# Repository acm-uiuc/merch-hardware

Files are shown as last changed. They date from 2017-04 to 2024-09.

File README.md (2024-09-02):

# Hardware to make Merch function



All the designs for the hardware components of Merch are found here.

## Components

### Vending Machine

This machine is a Dixie Narco 5800 Bevmax **4**, **not a Bevmax 3 machine**.

### Merch Hat

This unofficial Raspberry-Pi Hat allows a Pi to emulate keypresses on the machine's keypad.

### iPad Mount

### Connection Pictures

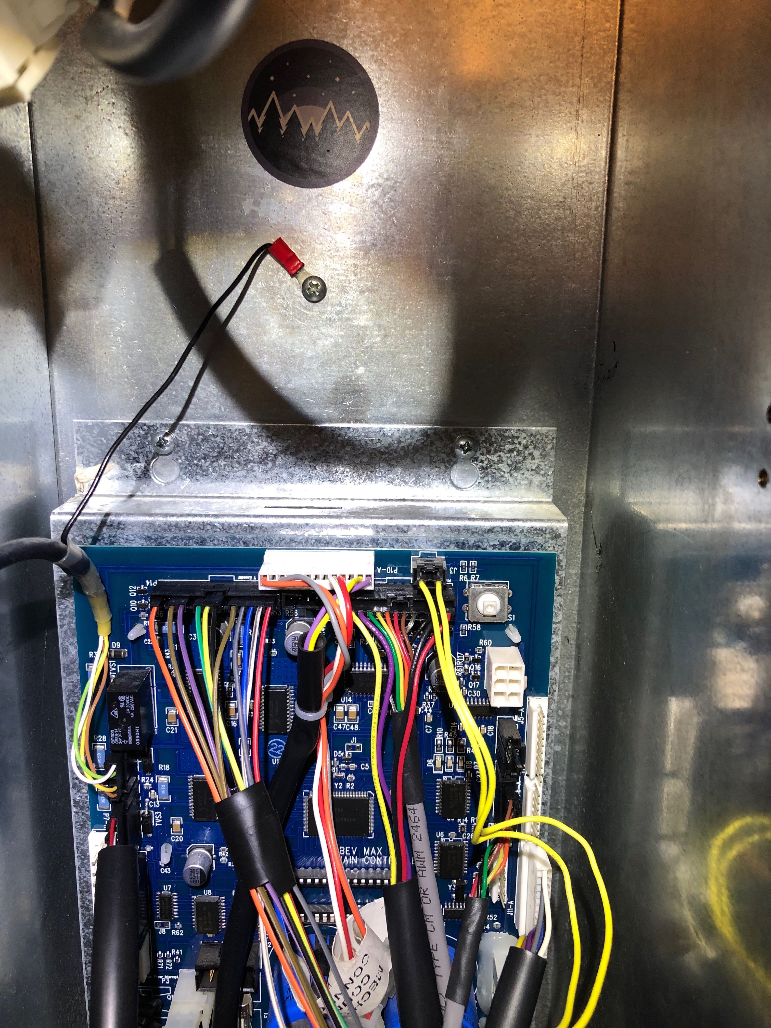
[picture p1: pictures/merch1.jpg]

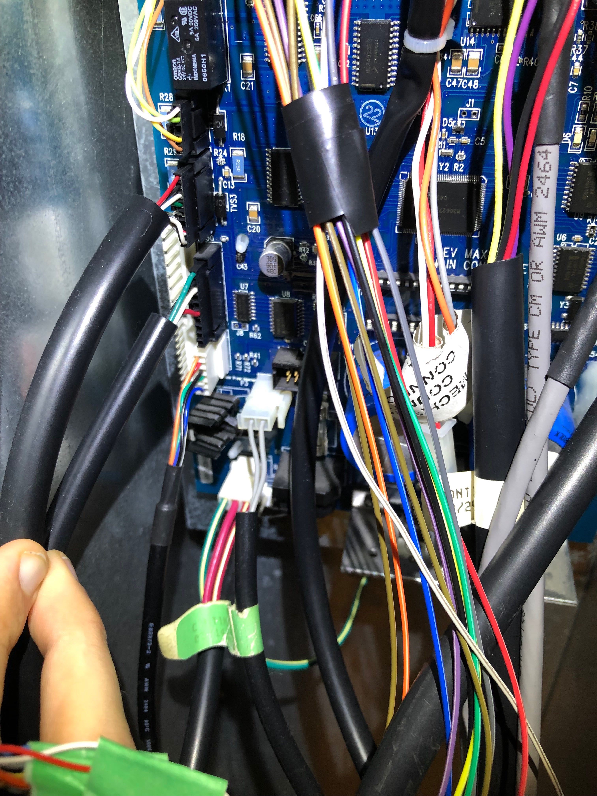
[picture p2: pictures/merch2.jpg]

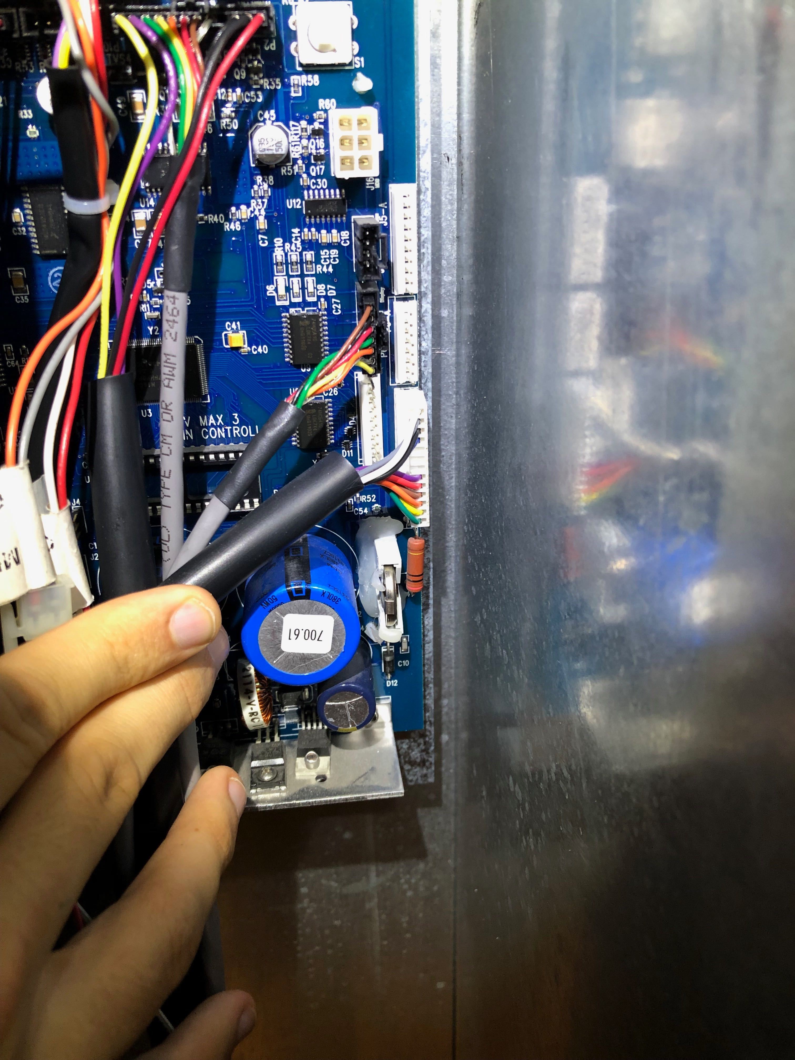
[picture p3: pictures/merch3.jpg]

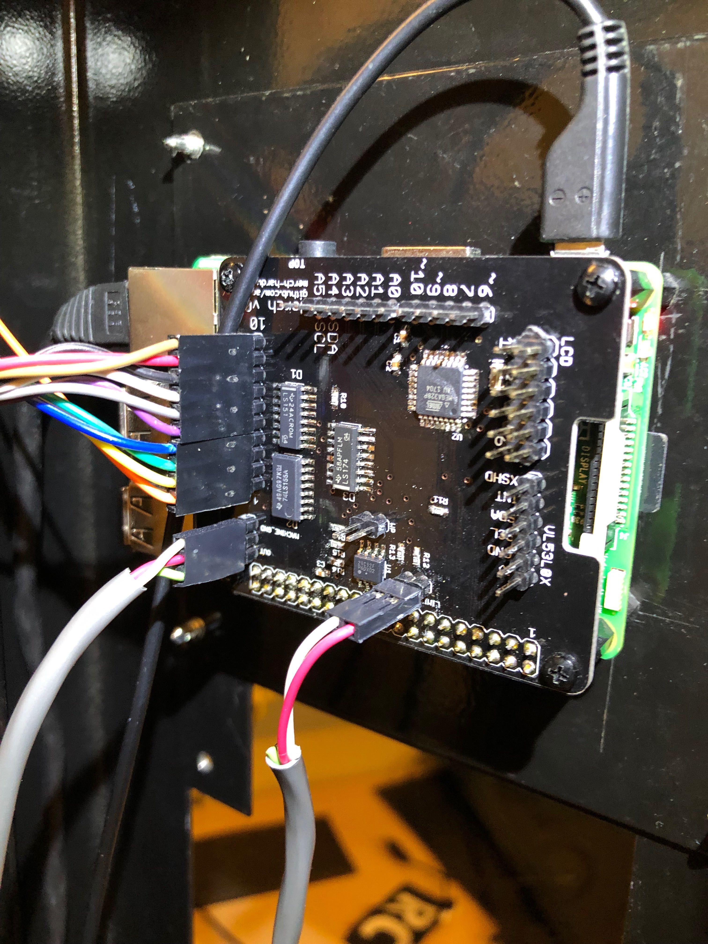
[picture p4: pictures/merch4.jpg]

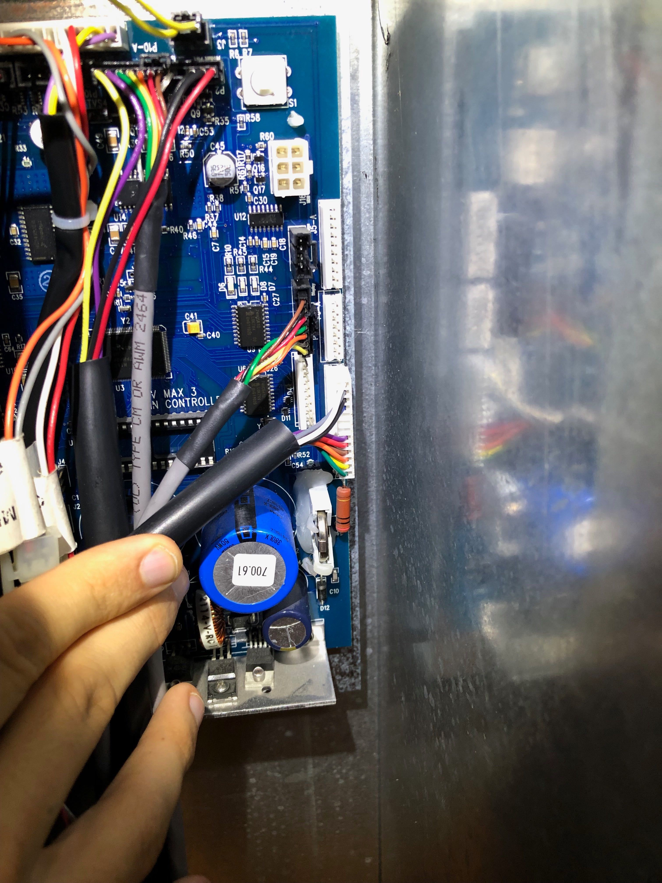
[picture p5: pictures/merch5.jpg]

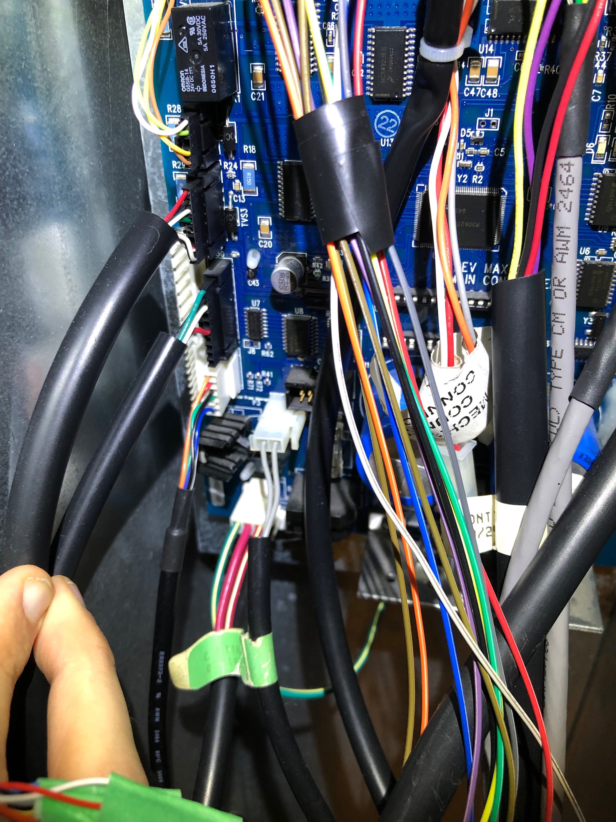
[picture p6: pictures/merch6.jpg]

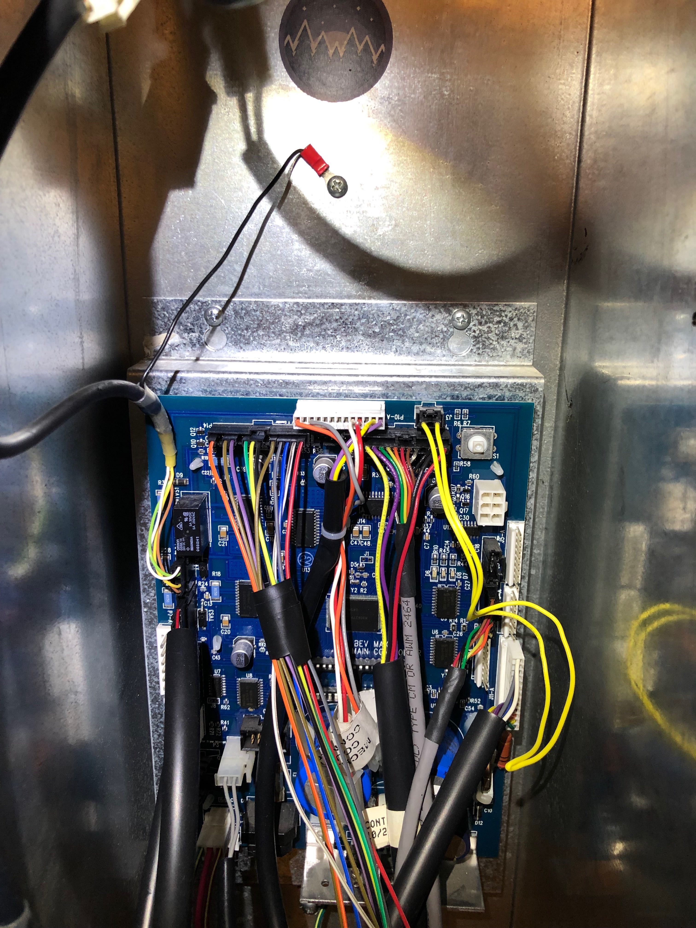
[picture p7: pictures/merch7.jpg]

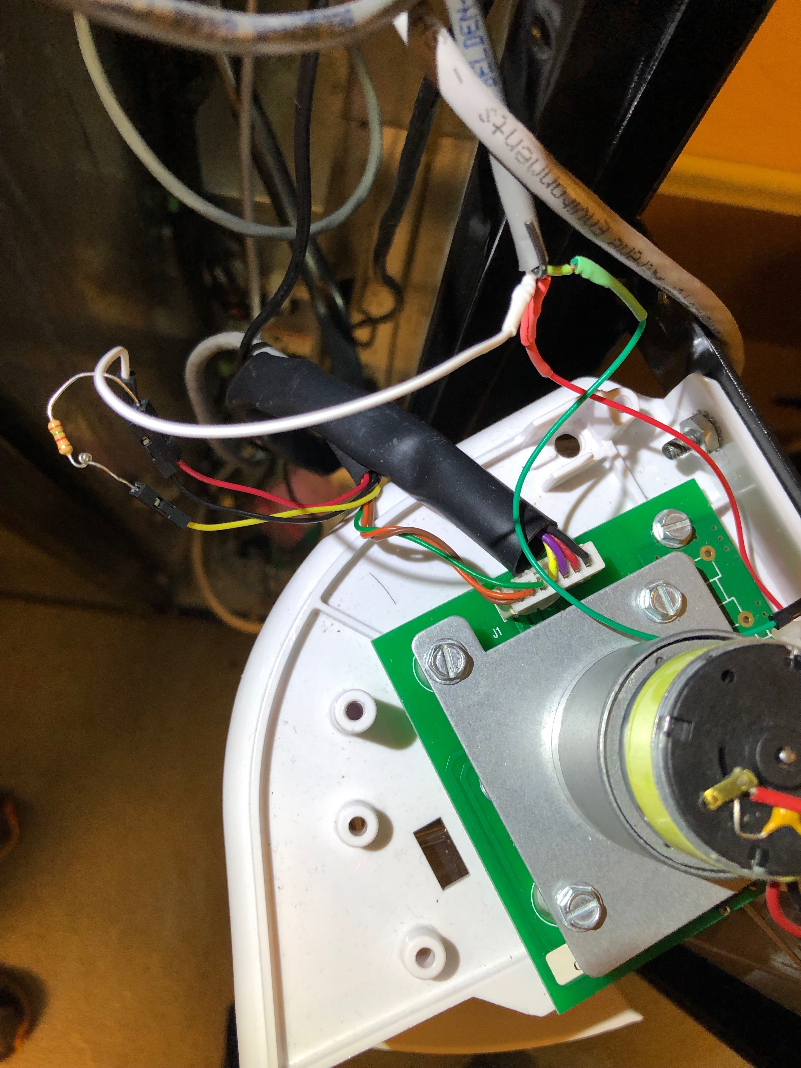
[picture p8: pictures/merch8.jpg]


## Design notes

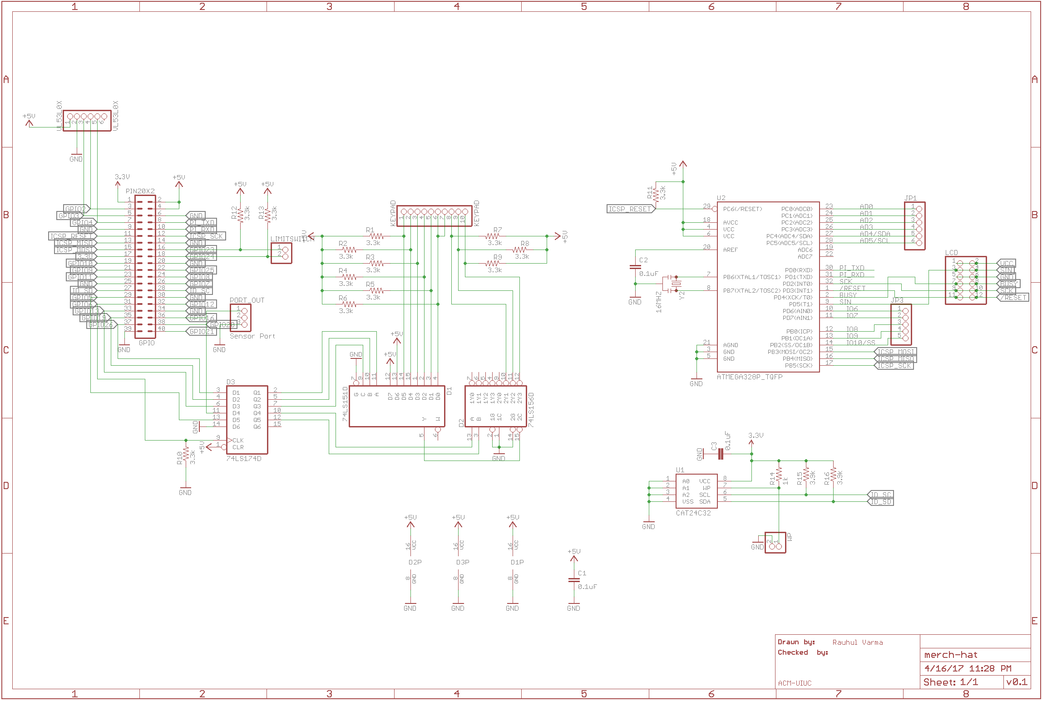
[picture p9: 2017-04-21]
keypad_pcb_surface_mount/Schematic.png

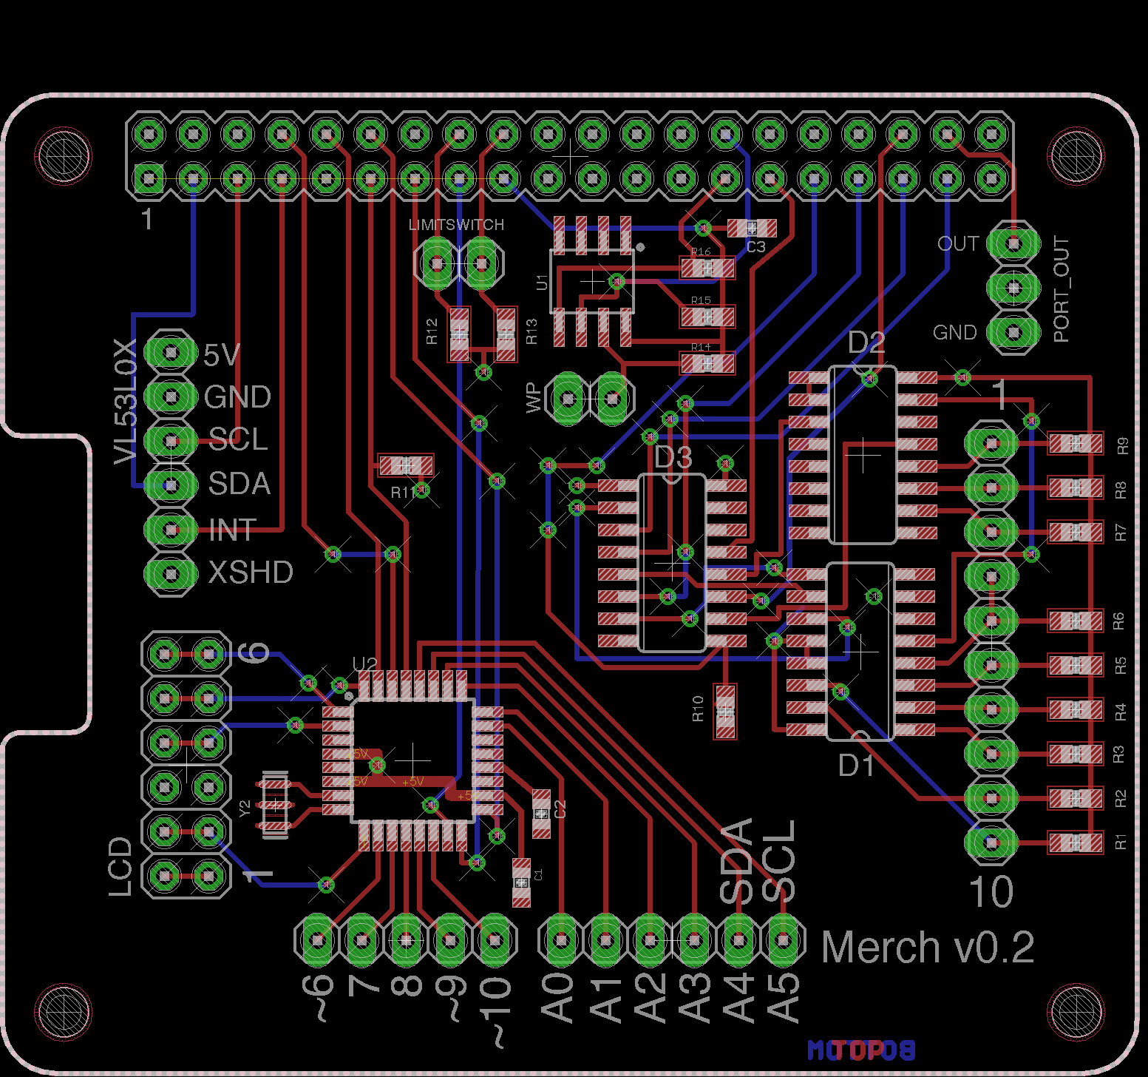
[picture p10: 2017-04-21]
keypad_pcb_surface_mount/BoardLayout.png

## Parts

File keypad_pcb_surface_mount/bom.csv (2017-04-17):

Location | MPN/Seeed SKU | Quantity
C1,C2,C3 | 302010138 | 3
R1,R2,R3,R4,R5,R6,R7,R8,R9,R10,R11,R12,R13 | 301010251 | 13
D1 | SN74LS151D | 1
D2 | SN74LS155D | 1
D3 | SN74LS174D | 1
R14 | 301010291 | 1
R15,R16 | RC0603JR-073K9L | 2
U1 | CAT24C32WI-G | 1
U2 | ATMEGA328P-AUR | 1
Y2 | CSTCE16MOV53-R0 | 1

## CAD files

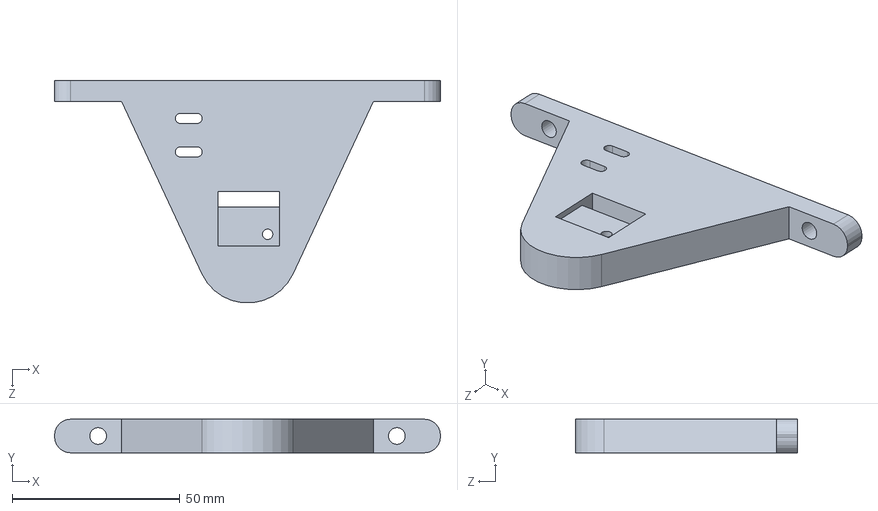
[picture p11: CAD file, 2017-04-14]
port_sensor_mount/sensor_mount.SLDPRT
115.0 x 10.0 x 66.3 mm

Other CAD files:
port_sensor_mount/sensor_mount.STL

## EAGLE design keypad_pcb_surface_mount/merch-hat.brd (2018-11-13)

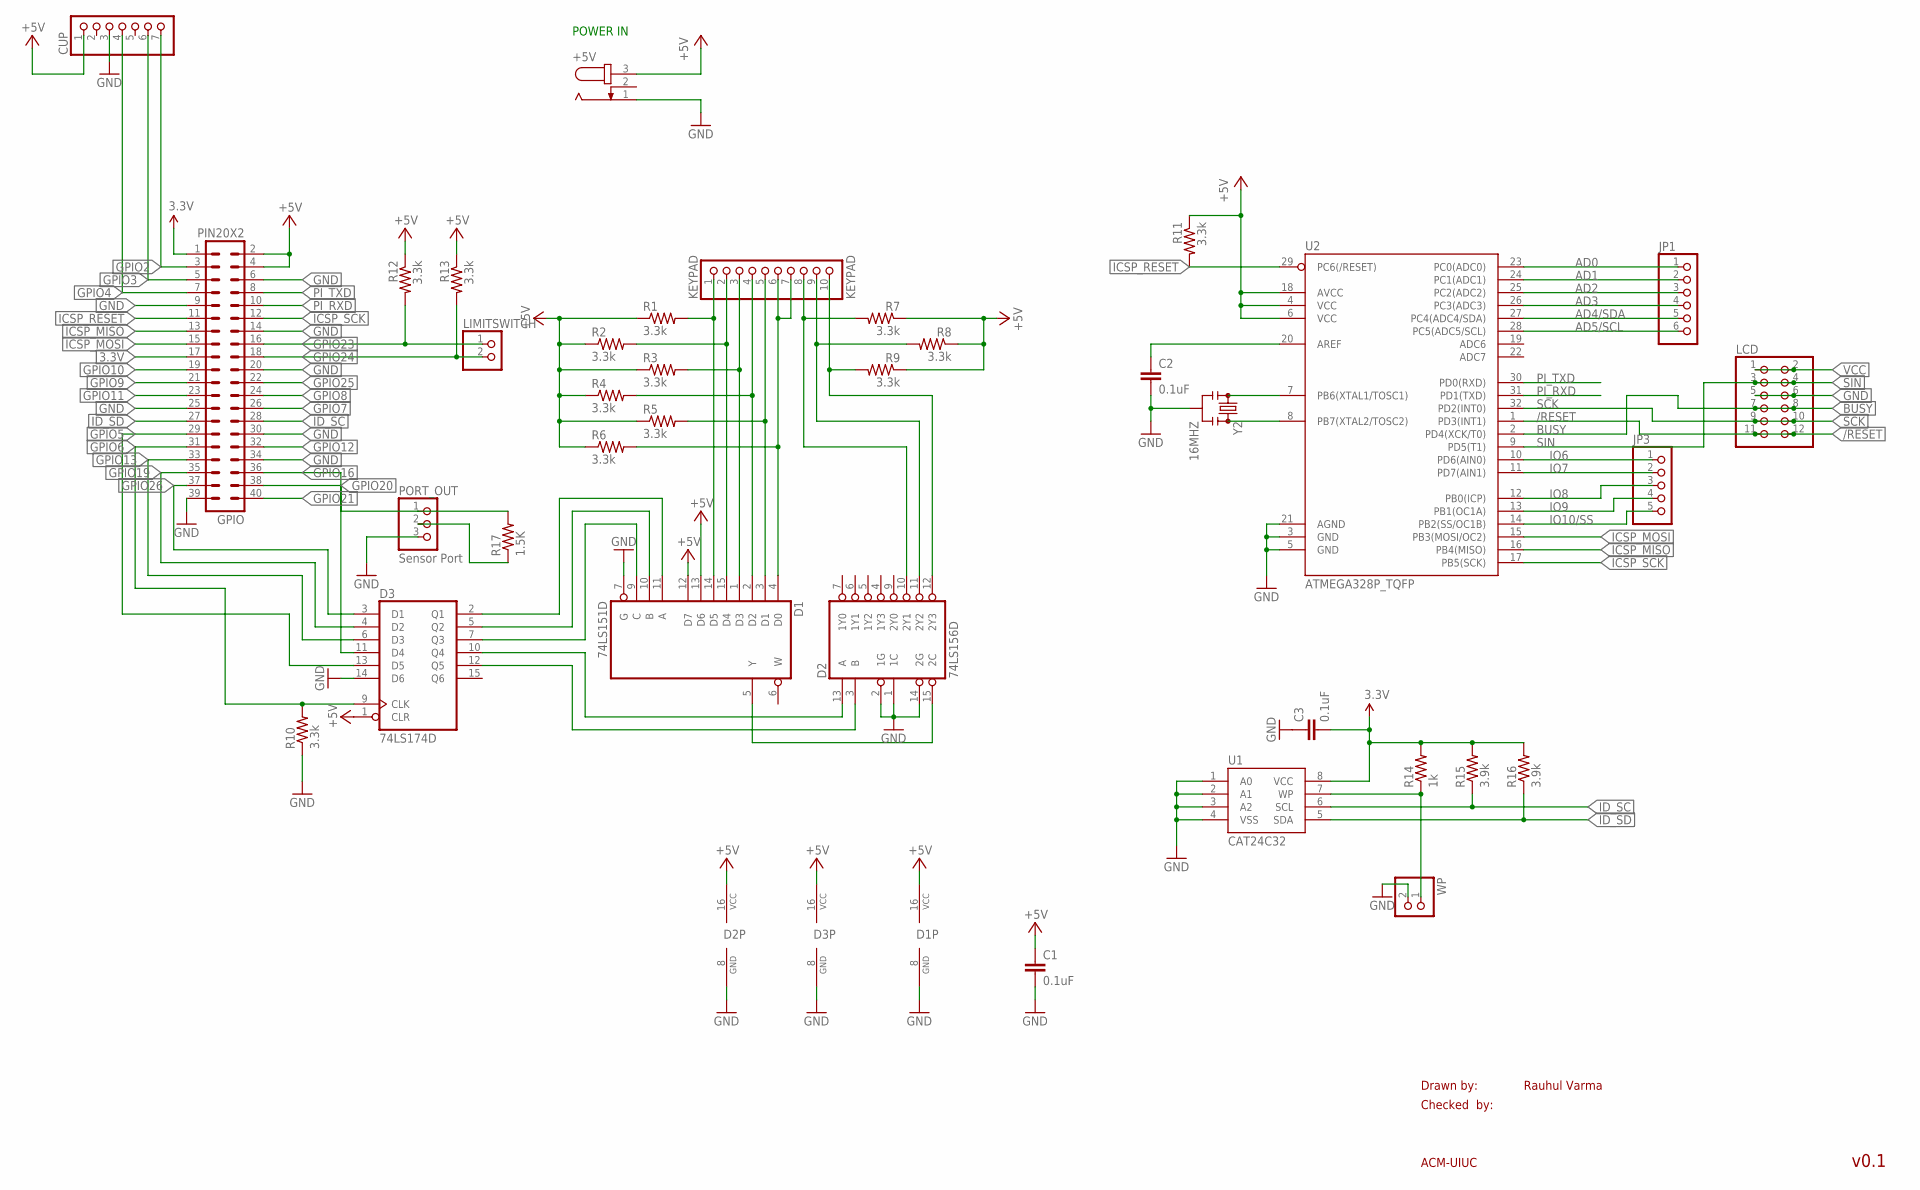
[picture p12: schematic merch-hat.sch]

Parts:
+5V: JACK-PLUG1; SPC4078
C1, C2, C3: 0.1uF; 0603-CAP
CUP: PINHD-1X7; 1X07
D1: 74LS151D; SO16
D2: 74LS156D; SO16
D3: 74LS174D; SO16
GPIO: PIN20X2; PIN_20X2
JP1: PINHD-1X6; 1X06
JP3: PINHD-1X5; 1X05
KEYPAD: KEYPAD; 1X10
LCD: PINHD-2X6; 2X06
LIMITSWITCH: PINHD-1X2; 1X02
PORT_OUT: Sensor Port; 1X03
R1, R2, R3, R4, R5, R6, R7, R8, R9, R10, R11, R12, R13: 3.3k; 0603-RES
R14: 1k; 0603-RES
R15, R16: 3.9k; 0603-RES
R17: 1.5K; R0603
U1: CAT24C32; SO08
U2: ATMEGA328P_TQFP; TQFP32-08
WP: PINHD-1X2; 1X02
Y2: 16MHZ; RESONATOR-SMD

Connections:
3.3V: C3.2, GPIO.1, GPIO.17, R14.2, R15.2, R16.2, U1.8 (VCC)
+5V: +5V.3, C1.1, CUP.1, D1.12 (D7), D1.13 (D6), D1.16 (VCC), D2.16 (VCC), D3.1 (CLR), D3.16 (VCC), GPIO.2, GPIO.4, R1.1, R2.1, R3.1, R4.1, R5.1, R6.1, R7.1, R8.1, R9.1, R11.1, R12.1, R13.1, U2.4 (VCC), U2.6 (VCC), U2.18 (AVCC)
/RESET: LCD.11, LCD.12, U2.1 (PD3(INT1))
AD0: JP1.1, U2.23 (PC0(ADC0))
AD1: JP1.2, U2.24 (PC1(ADC1))
AD2: JP1.3, U2.25 (PC2(ADC2))
AD3: JP1.4, U2.26 (PC3(ADC3))
AD4/SDA: JP1.5, U2.27 (PC4(ADC4/SDA))
AD5/SCL: JP1.6, U2.28 (PC5(ADC5/SCL))
BUSY: LCD.7, LCD.8, U2.2 (PD4(XCK/T0))
GND: +5V.1, C1.2, C2.2, C3.1, CUP.3, D1.7 (G), D1.8 (GND), D2.1 (1C), D2.2 (1G), D2.8 (GND), D2.14 (2G), D3.8 (GND), D3.14 (D6), GPIO.6, GPIO.9, GPIO.14, GPIO.20, GPIO.25, GPIO.30, GPIO.34, GPIO.39, LCD.5, LCD.6, PORT_OUT.3, R10.1, U1.1 (A0), U1.2 (A1), U1.3 (A2), U1.4 (VSS), U2.3 (GND), U2.5 (GND), U2.21 (AGND), WP.2, Y2.2
GPIO2: CUP.7, GPIO.3
GPIO3: CUP.6, GPIO.5
GPIO4: CUP.4, GPIO.7
GPIO5: D3.13 (D5), GPIO.29
GPIO6: D3.9 (CLK), GPIO.31, R10.2
GPIO7: GPIO.26
GPIO8: GPIO.24
GPIO9: GPIO.21
GPIO10: GPIO.19
GPIO11: GPIO.23
GPIO12: GPIO.32
GPIO13: D3.6 (D3), GPIO.33
GPIO16: D3.11 (D4), GPIO.36
GPIO19: D3.4 (D2), GPIO.35
GPIO20: GPIO.38, PORT_OUT.1, R17.2
GPIO21: GPIO.40
GPIO23: GPIO.16, LIMITSWITCH.1, R12.2
GPIO24: GPIO.18, LIMITSWITCH.2, R13.2
GPIO25: GPIO.22
GPIO26: D3.3 (D1), GPIO.37
ICSP_MISO: GPIO.13, U2.16 (PB4(MISO))
ICSP_MOSI: GPIO.15, U2.15 (PB3(MOSI/OC2))
ICSP_RESET: GPIO.11, R11.2, U2.29 (PC6(/RESET))
ICSP_SCK: GPIO.12, U2.17 (PB5(SCK))
ID_SC: GPIO.28, R15.1, U1.6 (SCL)
ID_SD: GPIO.27, R16.1, U1.5 (SDA)
IO6: JP3.1, U2.10 (PD6(AIN0))
IO7: JP3.2, U2.11 (PD7(AIN1))
IO8: JP3.3, U2.12 (PB0(ICP))
IO9: JP3.4, U2.13 (PB1(OC1A))
IO10/SS: JP3.5, U2.14 (PB2(SS/OC1B))
unnamed: D1.14 (D5), KEYPAD.1, R1.2
unnamed: R14.1, U1.7 (WP), WP.1
unnamed: PORT_OUT.2, R17.1
unnamed: D1.15 (D4), KEYPAD.2, R2.2
unnamed: D1.1 (D3), KEYPAD.3, R3.2
unnamed: D1.2 (D2), KEYPAD.4, R4.2
unnamed: D1.3 (D1), KEYPAD.5, R5.2
unnamed: D1.11 (A), D3.2 (Q1)
unnamed: D1.4 (D0), KEYPAD.6, KEYPAD.7, R6.2
unnamed: D2.10 (2Y1), KEYPAD.8, R7.2
unnamed: D2.11 (2Y2), KEYPAD.9, R8.2
unnamed: D2.12 (2Y3), KEYPAD.10, R9.2
unnamed: D1.10 (B), D3.5 (Q2)
unnamed: D1.9 (C), D3.7 (Q3)
unnamed: D2.13 (A), D3.10 (Q4)
unnamed: D2.3 (B), D3.12 (Q5)
unnamed: D1.5 (Y), D2.15 (2C)
unnamed: U2.7 (PB6(XTAL1/TOSC1)), Y2.1
unnamed: U2.8 (PB7(XTAL2/TOSC2)), Y2.3
unnamed: C2.1, U2.20 (AREF)
PI_RXD: GPIO.10, U2.31 (PD1(TXD))
PI_TXD: GPIO.8, U2.30 (PD0(RXD))
SCK: LCD.9, LCD.10, U2.32 (PD2(INT0))
SIN: LCD.3, LCD.4, U2.9 (PD5(T1))
VCC: LCD.1, LCD.2

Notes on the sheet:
Drawn by:
Checked by:
ACM-UIUC
Rauhul Varma
v0.1
POWER IN

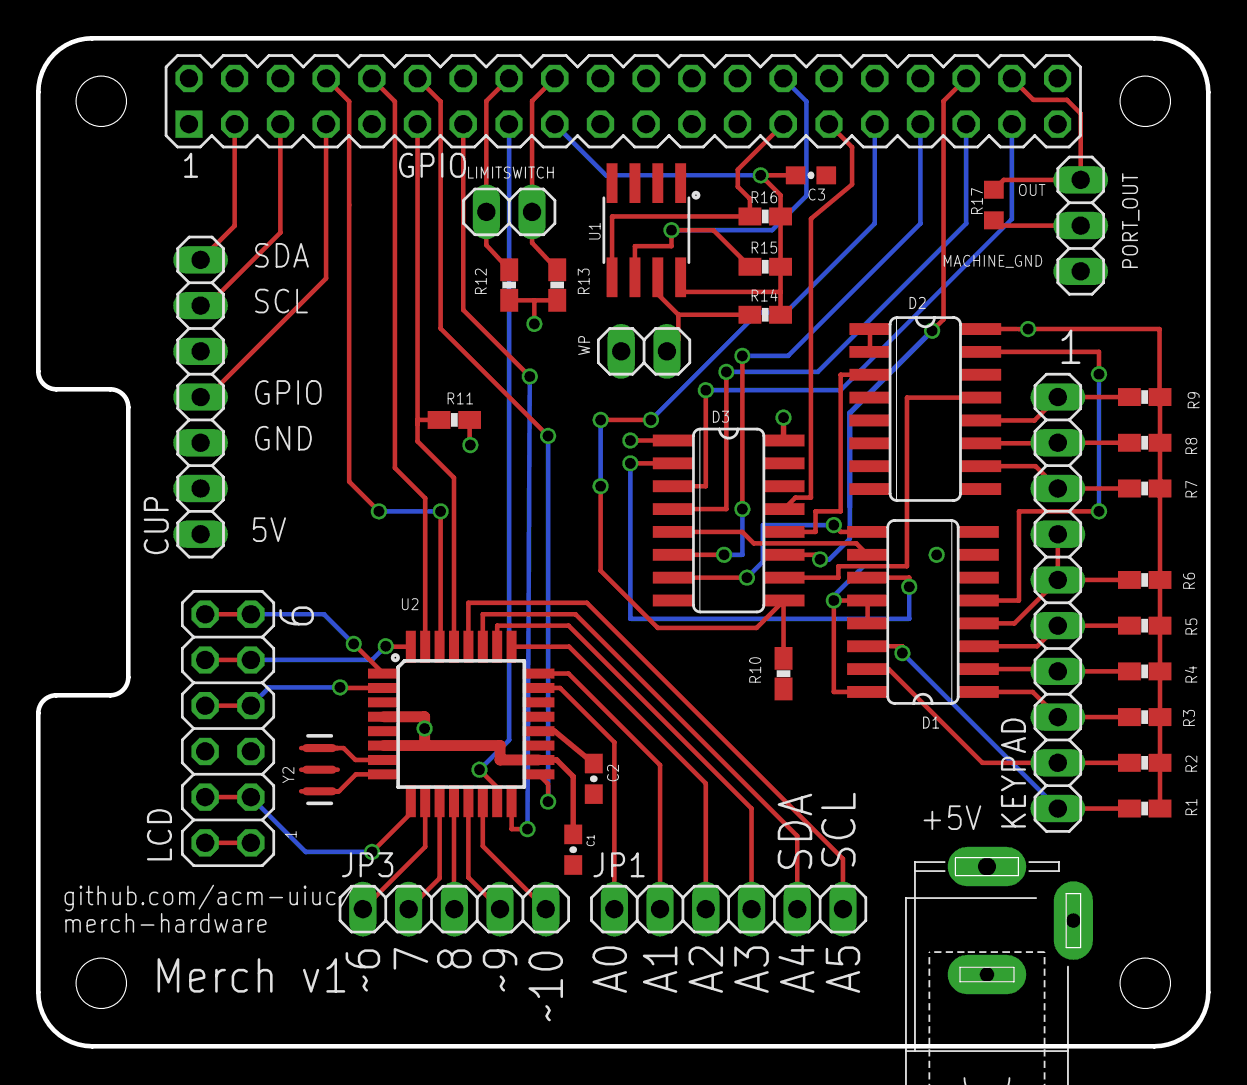
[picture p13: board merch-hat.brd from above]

Board: 2 copper layers, 65.0 x 56.0 mm, 36 parts (0 on the bottom side), 59 nets.

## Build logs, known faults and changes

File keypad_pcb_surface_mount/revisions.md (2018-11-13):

# Pending

# Done
- break out rpi power - maybe add barrel jack
- fix pinout for LoS sensor
- add pullup

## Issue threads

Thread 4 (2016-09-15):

Caffeine Feature Ideas

abrandemuehl, 2016-09-15:
Initial feature ideas:
- NFC and Magnetic stripe reader
  - How to add RFID? The cards use a HID tech
- Coin pay for non members - at higher price
- Touch screen
- Pressure sensors
- Leds everywhere inside
- Automatic Stock Notifications
- Auto purchase stock when empty
- Amazon echo/Voice control
- Data backed purchasing
- Variable pricing

Feel free to post any ideas you have here

Closed 2017-02-24.

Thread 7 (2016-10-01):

Interactive Side Panel Displays

rauhulvarma, 2016-10-01:
Replace the side panels with led arrays that responds to touches

Closed 2017-02-24.

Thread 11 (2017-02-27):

upload a pdf of the schematics and board layout

narendasan, 2017-02-27:
Can a pdf version of the schematics and board layout be included in this repo?

rauhulvarma, 2017-02-28:
uploaded board images in commit 6f4d541

Closed 2017-02-28.

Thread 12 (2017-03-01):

rename repo as merch-hardware

narendasan, 2017-03-01:
seeing as most of the stuff here is now to do with the new machine, I would rename this repo (so we dont loose anything) and track other projects on another one

rauhul, 2017-03-07:
renamed the repo to `Merch` in 98969d127c72997807c8939c8cea7637fbd40612

Closed 2017-03-07.

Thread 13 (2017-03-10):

Separate vending operation code and web server on machine

narendasan, 2017-03-10:
Can the code for operating the machine's arm be put into a separate library, instead of fiddling with Pi GPIO in route handlers, will let us throw away one or the other if we wish

abrandemuehl, 2017-03-13:
It would probably be worth splitting this into the "hat code", since the designs for the "hat" are in the repo as well

(Hat is in quotes since we don't technically have a true hat)

rauhul, 2017-03-22:
I dont know the standards for repo structure for a project like this. Would we have one repo for each component, i.e. iOS App, Pi hat, Pi code? How would you recommending splitting up the repo?

narendasan, 2017-03-22:
For repo structure I would recommend a separate repo for each component like groot (tagging them all merch will allow you to filter the other repos out). Might let you separate development more. This issue was more referring to things like https://github.com/acm-uiuc/Merch/blob/master/rPi_code/app.py#L23 where you are directly modifying GPIO states from a webserver. I would prefer having some library managing this and in the web server route being able to make a function call like Merch.vend("D2")

abrandemuehl, 2017-03-22:
We don't have to split it into separate repos, just make it so that the code for handling the gpio is done as library calls, instead of copy pasting it into the flask app

abrandemuehl, 2017-03-22:
I'll take a look at doing that

abrandemuehl, 2017-03-22:
I'm not sure the scope of the project is large enough to be worth separate repos

narendasan, 2017-03-22:
@abrandemuehl I think the library is a higher priority, but I think it might be worth separating the parts out because as development proceeds, ios devs wont care about the hardware specs, and the groot guys wont care about the ios code and ultimately we want to be in a position where any particular component can be replaced without the rest of the system breaking so creating expected abstract APIs for each component will be important. I would say make a team for merch development (and a gitter channel so random people can walk in and contribute) and have a bunch of repos you manage. I can help set that up as I did the same for groot. @rauhul @abrandemuehl let me know if you want me to set that up.

rauhul, 2017-03-22:
@narendasan yeah, you could set it up please.

abrandemuehl, 2017-03-22:
Okay, sounds good

narendasan, 2017-03-22:
Closing and moving issue about separation of GPIO code and webserver to acm-uiuc/merch-embedded

Closed 2017-03-22.

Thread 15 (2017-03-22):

add license headers to all the source files in hardware

narendasan, 2017-03-22:
pre-append the following header to the file as a comment to all source files:

```
Copyright © 2017, ACM@UIUC

This file is part of the Merch Project.

The Merch Project is open source software, released under the University of Illinois/NCSA Open Source License.
You should have received a copy of this license in a file with the distribution.
```

rauhul, 2017-04-14:
How would we implement this

narendasan, 2017-04-14:
let me look into open hardware practices

narendasan, 2017-04-14:
ok so we have a couple options
we can use the NCSA license though its a software license which seems fine (Arduino uses GPL)
or we can use CC-by-SA which people use on hardware projects
as to how to add it, a file called ```LICENSE``` should be sufficient

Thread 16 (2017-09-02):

Floating GPIO Pins

rauhul, 2017-09-02:
Currently after making a digital keypress the pi's gpio pins take on ~1.3v when they should be low (0v).

Not known if this is a manufacturing issue or a design bug.

abrandemuehl, 2017-09-02:
Raspberry PI has internal pull resistors. We can use them by using a third argument in the pin setup function
Example: `GPIO.setup(17, GPIO.IN, pull_up_down=GPIO.PUD_UP)`

Reference: https://learn.sparkfun.com/tutorials/raspberry-gpio/python-rpigpio-api

abrandemuehl, 2017-09-02:
What ground is that 1.3v referenced to?

rauhul, 2017-09-02:
The machine and the rpi share a ground

rauhul, 2017-09-05:
This bug appeared due to incorrect testing methodology. Since the test vend script only assigns value to rPi's GPIO pins while its running (i.e. the take no value after the script has ended), we see floating values on these pins.

This appears to the root cause of the vend failures and various other bugs.

narendasan, 2017-09-05:
But we tested in console without the script as well, didn't we detect the issue there (don't remember myself)? Have we tested with the server? Also shouldn't tear down of the gpio library address floating values on the gpio? It seems there is still inconsistent behavior (unless you have tested the boards more formally than running in console and with the sample script). We should also make sure the test script is modified to be more close to how the server will work.

narendasan, 2017-09-05:
If it is indeed an issue with cleanup, then the bug is testing will appear in  app.py as well. Root cause is that the Python interpreter does not guarantee that destructors of global instances will be called when the app terminates. It is in the destructor of merch that we call GPIO.cleanup. Since both app.py and vend_merch use a global instance, floating GPIO should be expected with both. The solution is to initialize execution in a context (using with) and changing the __del__ method to __exit__. Source: https://stackoverflow.com/questions/3554952/del-at-program-end. I am still not convinced this address vend failures with the new board

Closed 2017-09-05.

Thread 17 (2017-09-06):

Explore getting machine state directly from control board

rauhul, 2017-09-06:
As the title suggests, we would like to find a way to know what the machine is currently doing from some pins exported from the control board.

narendasan, 2017-09-07:
Or some sort of diagnostic system (e.g. LEDs)

pwk2, 2017-09-12:
Most relevent/potentially helpful thing to tracking the machine state I found were P3 P4 switches which hold the information of if the Picker is HOME/OUT, respectively. I believe this to be the way the vending machine controls machine state.
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

pwk2, 2017-09-14:
After hours or reading and searching, xy limit seem to be the way to go.

Closed 2017-09-14.

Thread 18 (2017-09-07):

Add port vend sensor mount to source control

rauhul, 2017-09-07:
The 3D model for this part currently lives on some computer in ACM and need to be tracked in this repo.

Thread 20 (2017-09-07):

Breakout machine limit switch signals

rauhul, 2017-09-07:
Find the limit switch signal wires in Merch, spilt them so the rPi can observe this values.

pwk2, 2017-09-14:
Y-limit was wrong, correct one has been labeled.

Will now be splitting the wires, does ACM have inline splices or should i join them manually?

I observed the voltage on the two limit switches to be 4.94 on the "20" setting for the multimeter. I don't know if this means ~5 volts or ~10 volts but in either case that voltage will be too much for the RPi, will need help in dealing with that issue.

abrandemuehl, 2017-09-14:
Chances are that the limit switch is just a continuity line. Either it is pulled to ground when it is pressed, or it is pulled to power.

You'd have to do some more continuity testing for the limit switches.

pwk2, 2017-09-19:
I tested the voltage in the x and y limit switch wires(from motor board to control board) when the motors pull the merch picker to its home position (bottom left). They give no volt reading until the picker reaches the base x or base y (for their respected wires), and then once it is at x=0 or y=0 it gives a constant reading of 4.94 even when the motors are released. So constant voltage indicates that the picker is home, this is sufficient to tracking machine state. Should I split the wires now?

abrandemuehl, 2017-09-19:
Just curious, when you say "even when the motors are released", what do you mean?

pwk2, 2017-09-19:
When they aren't turning, when the machine isn't giving them power, sorry I'm bad at putting names on things.

abrandemuehl, 2017-09-19:
Okay. Makes sense then. The limit switches get pressed when the machine moves to 0,0 and stay pressed until the machine moves away. The limit switches don't really push back, so they won't push the machine off of them.

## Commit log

2017-04-10 Move Keypad, Add Port Sensor
    [merch-hat.brd, merch-hat.sch]
2017-04-14 Finish Up Surface Mount Version
    [merch-hat.brd, merch-hat.sch]
2017-04-14 add decoupling cap
    [merch-hat.brd, merch-hat.sch]
2017-04-14 Add Limit Switch Interface
    [merch-hat.brd, merch-hat.sch]
2017-04-14 Add Port Sensor Labels
    [merch-hat.brd, merch-hat.sch]
2017-04-14 Minor fixes
    [merch-hat.brd]
2017-04-14 Add Custom port sensor mount
    [sensor_mount.SLDPRT, sensor_mount.STL]
2017-04-14 Add gerber and dru files for seeedstudio
    [merch-hat.brd]
2017-04-17 Fixes and updates
    [bom.csv, merch-hat.brd, merch-hat.sch]
2017-04-17 Change label, make vias circles
    [merch-hat.brd]
2017-04-19 Connect airwire
    [merch-hat.brd]
2017-04-19 Add png and github link
    [merch-hat.brd]
2017-04-21 fix misaligned routes, make all vias round, update board images
    [merch-hat.brd]
2018-11-13 add power connctor, new range sensor pinout, pullup
    [merch-hat.brd, merch-hat.sch]

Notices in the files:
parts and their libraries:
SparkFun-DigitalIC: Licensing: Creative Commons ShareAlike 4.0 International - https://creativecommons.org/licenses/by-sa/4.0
